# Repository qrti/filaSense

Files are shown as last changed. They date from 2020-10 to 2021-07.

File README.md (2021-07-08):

# **Optical Filament Runout Sensor**

Optical filament detection is not as easy as it seems at first glance. Especially transparent filaments might focus emitter-LED light and even enhance detection levels instead of dampen them as opaque filaments do. As a consequence this is a 'change of condition sensor' that detects runout of filament but not the presence or absence of it. Nevertheless the detection of some transparent filaments is possibly not reliable.

<br>

## Operation
The sensors state of operation is indicated by a LED. After a filament runout (or load) happens, the sensor reports it by a two second pulse to the 3d-printer and the LED starts long-blinking until the button is pressed.

### LED
- **constantly on**  
sensor online
- **short blink**  
sensor offline
- **long blink**  
filament runout (or load) detected

### Button
- **if sensor is online or offline**  
toggle online/offline
- **if a change was detected**  
make sensor online

### Source
- be sure to set ATTINY13 fuses as documented in source comments
- change the detection logic
```
.define     LOGIC       0               ;0 LOW or 1 HIGH means detection for 3d-printer
```
- dampen detection level by rising SLCY
```
.equ    SLSCY       =   22              ;t = SLSCY * ct * 256, slow service cycle                           
```

<br>

---

<br>

## Views

ready mounted sensor   
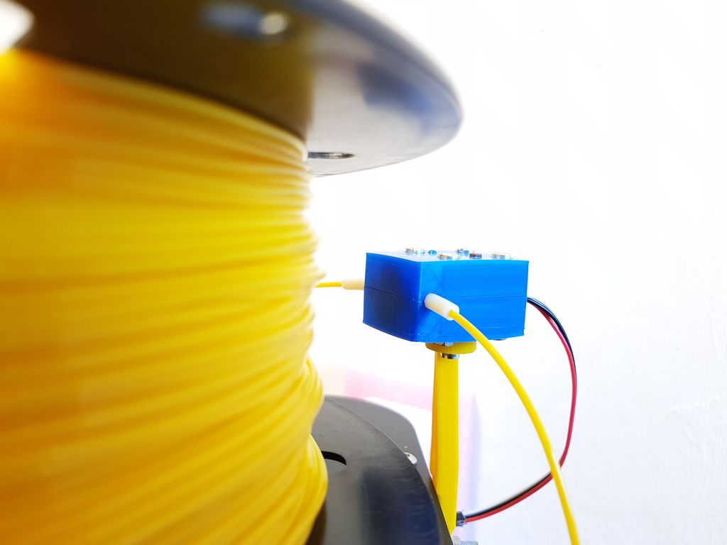
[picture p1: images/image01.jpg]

<br>
<br>

the filament teflon tube has to be exactly in the optical axis of the slotted optical sensor   
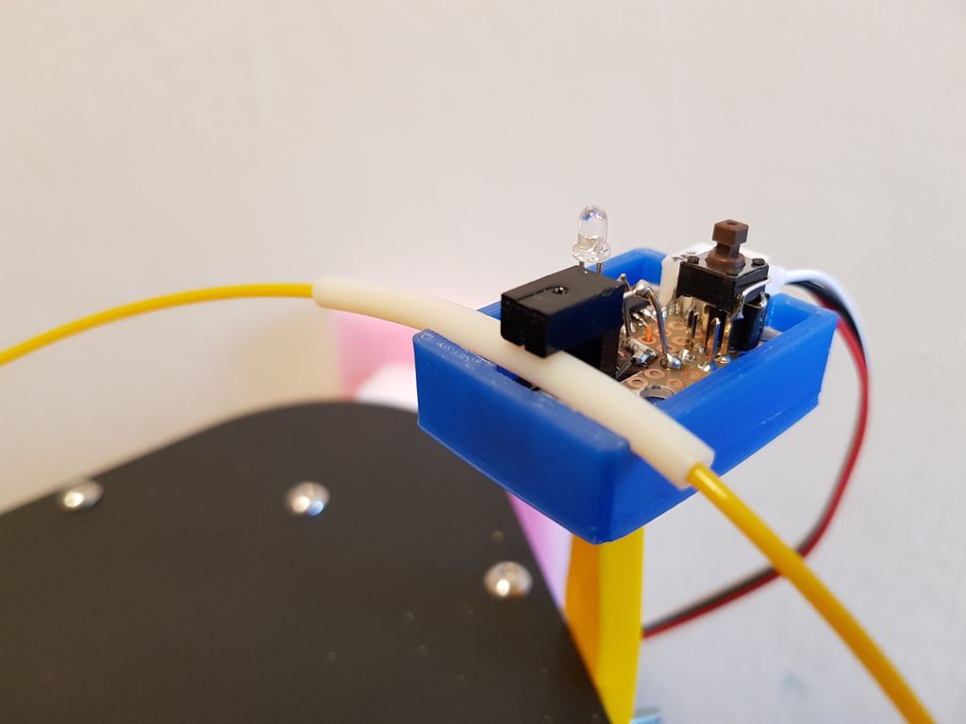
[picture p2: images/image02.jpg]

<br>
<br>

teflon tube removed   
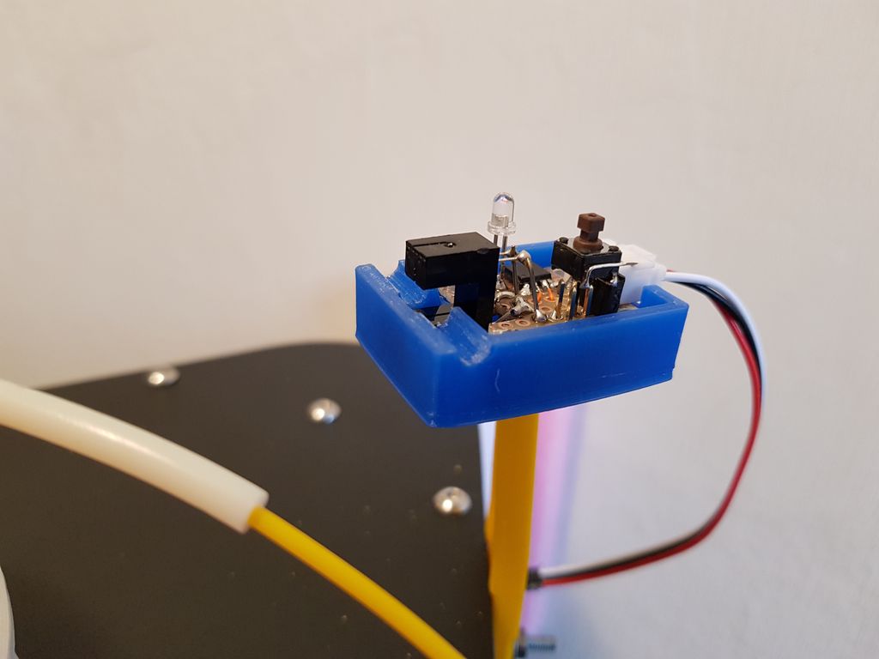
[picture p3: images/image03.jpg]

<br>
<br>

hand wired prototype, the push-button is removable to allow in circuit programming of the ATTINY13 controller   
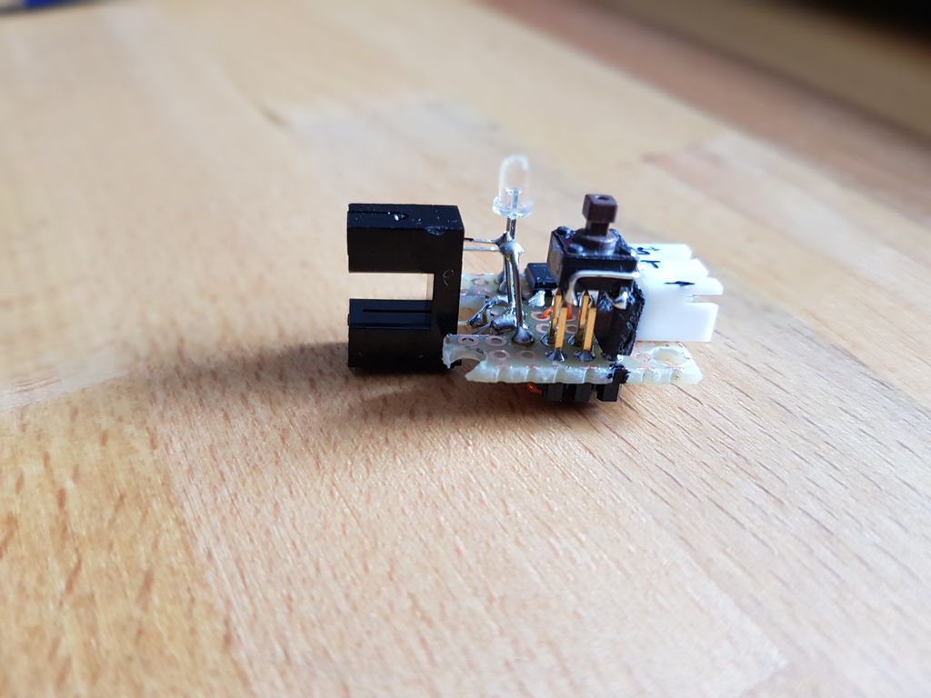
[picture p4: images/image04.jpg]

<br>
<br>

3d-print files in stl format are in the repository   
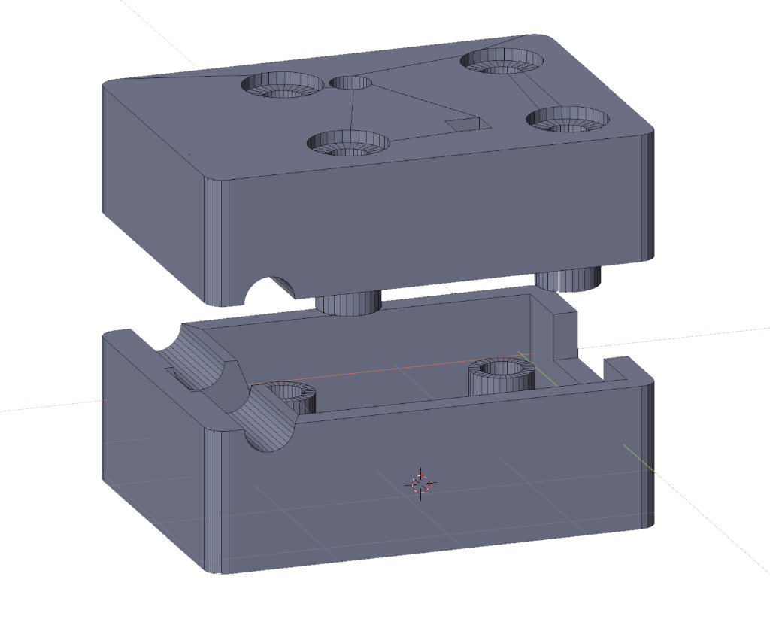
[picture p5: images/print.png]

<br>
<br>

schematic   
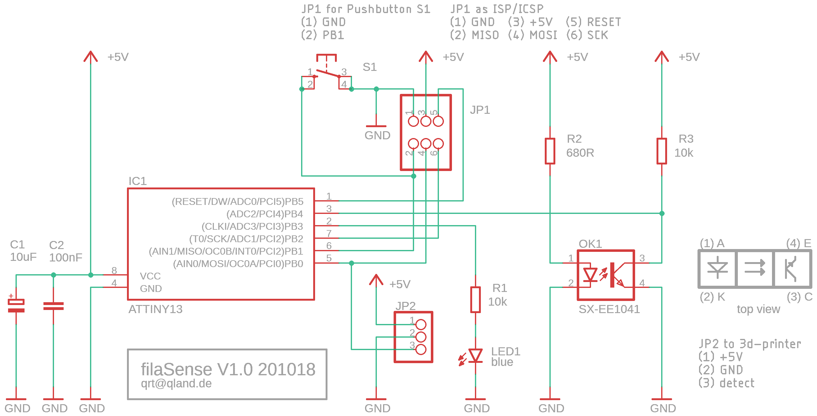
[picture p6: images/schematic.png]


<br>
<br>

---

[qrt@qland.de](mailto:qrt@qland.de) 210708

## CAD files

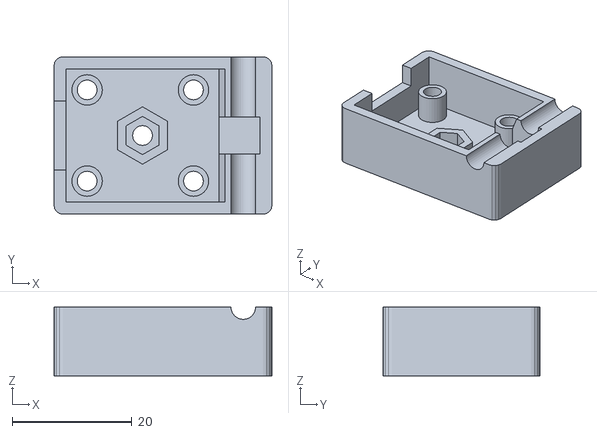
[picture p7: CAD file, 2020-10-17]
stl/sensebox_box_bot.stl
36.5 x 26.3 x 11.5

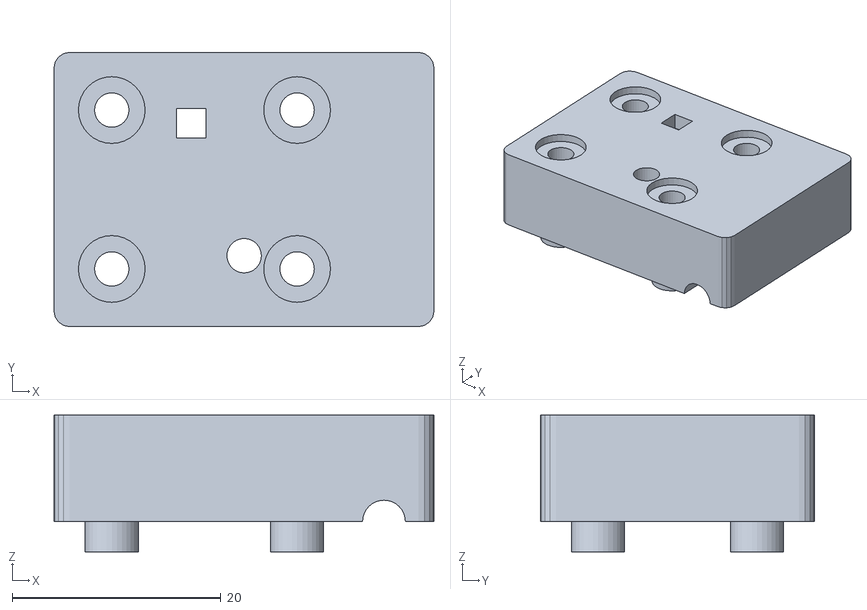
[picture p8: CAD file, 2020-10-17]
stl/sensebox_box_top.stl
36.5 x 26.3 x 13.1

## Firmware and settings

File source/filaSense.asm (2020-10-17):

;filaSense.asm V0.7 201007 qrt@qland.de 
;
;ATTINY13 - - - - - - - - - - - - - - - - - - - - - - - - - -
;fuse bits     43210   high
;SELFPRGEN     1||||   (default off)
;DWEN           1|||   (default off)
;BODLEVEL1..0    11|   (default off) (drains power in sleep mode)
;RSTDISBL          1   (default off)
;              11111
;
;fuse bits  76543210   low
;SPIEN      0|||||||   (default on)
;EESAVE      1||||||   (default off)
;WDTON        1|||||   (default off) (watchdog force system reset mode)
;CKDIV8        1||||   no clock div during startup
;SUT1..0        10||   64 ms + 14 CK startup (default)
;CKSEL1..0        01   4.8 MHz system clock
;           01111001

;-------------------------------------------------------------------------------

;V0.5   mid level capacitor 
;V0.6   soft mid level
;V0.7   logic define

;todo

;-------------------------------------------------------------------------------

;.device ATtiny13
.include "tn13def.inc"

;-------------------------------------------------------------------------------

.define     LOGIC       0               ;0 LOW, 1 HIGH = means detection

;-------------------------------------------------------------------------------

.cseg
.org $0000
rjmp main                                ;Reset Handler
;.org $0001
;rjmp EXT_INT0                           ;External Interrupt0 Handler
;.org $0002
;rjmp PCINT0                             ;Pin Change Interrrupt Handler
;.org $0003
;rjmp TIM0_OVF                           ;Timer0 Overflow Handler
;.org $0004
;rjmp EE_RDY                             ;EEPROM Ready Handler
;.org $0005
;rjmp ANA_COMP                           ;Analog Comparator Handler
;.org $0006
;rjmp TIM0_COMPA                         ;Timer0 Compare A
;.org $0007
;rjmp TIM0_COMPB                         ;Timer0 CompareB Handler
;.org $0008
;rjmp WATCHDOG                           ;Watchdog Interrupt Handler
;.org $0009
;rjmp ADC                                ;ADC Conversion Handler

;-------------------------------------------------------------------------------

.def    a0          =   r0              ;main registers set a
.def    a1          =   r1
.def    a2          =   r2
.def    a3          =   r3
.def    a4          =   r16             ;main registers set a immediate
.def    a5          =   r17
.def    a6          =   r18
.def    a7          =   r19

.def    FLAGR       =   r29             ;flag register          YH
.def    NULR        =   r31             ;NULL value register    ZH

;-------------------------------------------------------------------------------

.def    sumFL       =   r4              ;fast average
.def    sumFH       =   r5
.def    avgF        =   r6

.def    sumSL       =   r7              ;slow mid average
.def    sumSH       =   r8
.def    avgS        =   r9

.def    ledbt       =   r20             ;led blinc ticker
.def    slsc        =   r21             ;slow service counter

.def    thclo       =   r10             ;min threshold row counter low
.def    thchi       =   r11             ;                          high

.def    foscL       =   r24             ;filament out signal counter
.def    foscH       =   r25

;-------------------------------------------------------------------------------
;abused IO registers
.equ    FLAGS0      =   ACSR            ;flags 0
.equ    UNUF00      =   ACIS0           ;unused
.equ    UNUF01      =   ACIS1           ;

.equ    FLAGS1      =   WDTCR           ;flags 1
.equ    UNUF10      =   WDP0            ;unused
.equ    UNUF11      =   WDP1            ;
.equ    UNUF12      =   WDP2            ;

;flags in FLAGR
.equ    DETOFF      =   0               ;detection off
.equ    FIOUM       =   1               ;filament out memo
.equ    KEYPR       =   2               ;key pressed memo

;-------------------------------------------------------------------------------

.equ    CTRP        =   PORTB           ;control port
.equ    CTRD        =   DDRB            ;        ddr
.equ    CTRI        =   PINB            ;        pinport
.equ    FOUT        =   PINB0           ;        filament out           out (MOSI)
.equ    KEY         =   PINB1           ;        key                        (MISO)
.equ    UNUP2       =   PINB2           ;        unused                     (SCK)
.equ    LED         =   PINB3           ;        LED                    out
.equ    ADIN        =   PINB4           ;        AD input               in  (ADC2)
.equ    UNUP5       =   PINB5           ;        unused                     (RESET)

;                         ..-al-ko      a adin, l led, k key, o fout
;                         ..-IO-IO      I input, O output, . not present, - unused
.equ    DDRBM       =   0b00001001      
.if LOGIC == 0
;                         ..-NH-PH      L low, H high, P pullup, N no pullup
.equ    PORTBM      =   0b00001010
.elif LOGIC == 1
;                         ..-NH-PL  
.equ    PORTBM      =   0b00001010
.endif

;-------------------------------------------------------------------------------
;AD frequency (10 bit, target 50..200 kHz)      4.8E6 / 64 = 75E-3
;conversion time                                75E3^-1 * 13 = 173.333 us   (ct)
;
.equ    ADMUXC      =   (1<<ADLAR|1<<MUX1)                              ;left adjust, ADC2 PB4, Ref Vcc
.equ    ADCSRAC     =   (1<<ADEN|1<<ADSC|1<<ADATE|1<<ADPS2|1<<ADPS1)    ;ADC enable, start, auto (free running -> ADSCRB), div 64
.equ    DIDR0C      =   (1<<ADC2D)                                      ;ADC2 digital input buffer off

.equ    FOSDU       =   11538               ;2 s / ct               filament out signal duration
.equ    SLSCY       =   22                  ;t = SLSCY * ct * 256   slow service cycle                           

.equ    ADVTH       =   32                  ;1 AD = 5/255 = 1/51 ~ 0.0196 V
.equ    MINTHR      =   4                   ;min threshold row

;-------------------------------------------------------------------------------

main:
        ldi     a4,low(RAMEND)              ;set stack pointer
        out     SPL,a4                      ;to top of RAM

        ldi     a4,PORTBM                   ;port B
        out     PORTB,a4
        ldi     a4,DDRBM                    ;ddr B
        out     DDRB,a4

        sbi     ACSR,ACD                    ;comparator off

;- - - - - - - - - - - - - - - - - - - -

        clr     NULR                        ;init NULR (ZH)
        ldi     ZL,29                       ;reset registers
        st      Z,NULR                      ;store indirect
        dec     ZL                          ;decrement address
        brpl    PC-2                        ;r0..29 = 0, ZL = $ff, ZH = 0 (NULR)

        ldi     ZL,low(SRAM_START)          ;clear SRAM
        st      Z+,NULR
        cpi     ZL,low(RAMEND)
        brne    PC-2

        ldi     slsc,SLSCY                  ;init slow average loop counter     
        ldi     foscL,low(FOSDU/2)          ;set signal counter
        ldi     foscH,high(FOSDU/2)
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
